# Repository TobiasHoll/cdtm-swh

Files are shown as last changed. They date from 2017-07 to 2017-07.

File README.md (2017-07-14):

# Interactive Beerpong Table (Single Player)

An interactive beerpong game that allows to play beerpong in an arcade game style.

## Description
The interactive beerpong table allows a player to play beerpong (without actual beer) in a normal beerpong set-up. The game is for single players (or players taking turns), because only one side of the beerpong table is built.
A green light within the cups indicates where the player needs to hit. If he succeeds, an alcohol shot is released automatically from the dispenser. Different game logics can be programmed in order to have different levels of difficulties.

## Gameplay

3 cups are lit up green and 7 are lit up red. The cups colours change every 4 secods to make it more difficult. If you hit a green cup, a shot is dispensed. If not you can throw again (3 balls normally)

<p align="center"><a href="https://www.youtube.com/watch?v=cWcqSVTLIn0">
  Beerpong-machine
</a></p>

## Components and where to get them
### Beerpong Box
* Hardware
    * [Arduino](https://store.arduino.cc/arduino-leonardo-with-headers)
    * [Additional 5V Power source](https://www.sparkfun.com/products/12977)
    * [Breadboard](https://www.sparkfun.com/products/12615)
    * [LEDs to light up the cups](http://www.ebay.com/itm/10-1000pcs-WS2812B-5050-RGB-LED-no-PCB-Board-1-LED-Module-Pixel-Light-5V-/221989107317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)
    * [Infra-red sensor for ball detection](https://www.ebay.com/p/10pcs-IR-Infrared-Obstacle-Avoidance-Sensor-Module-for-Arduino-Smart-Car-Robot/1149951524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)
    * [A lot of wires](https://www.conrad.de/de/raspberry-pi-verbindungskabel-rb-cb1-25-1192229.html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)
* Material
    * Wooden panels (2x 45cm*40cm, 1x 40cm*40c)
    * Additional Power Source for the Stepper (depends on the stepper, we used an old ac-adapter)
    
* Material
    * Wooden panels (2x 45cm\*40cm, 1x 40cm\*40cm, 1x 39cm\*40cm)
    * Wooden blocks (4x 5cm\*5cm\*15cm)
    * Lego Technics (check out the video)

## Assembly of the Beerpong-box

Check out the [Youtube video](https://www.youtube.com/watch?v=cWcqSVTLIn0) to see how it's built. This should provide you with enough details, so you can reproduce it.

### Cups (repeat this 10 times) 
* Wire up 3 LEDS per cup
* Remove the bottom of the cup and make 3 holes for the LEDs into it (We used a hot needle)
* Attach the LEDs with hot glue
* Remove the head and the bottom from one bottle
* Make a hole into the side of the bottle (for the sensor)
* Attach the bottle to the bottom of the cup with hot glue
* Attach the IR-Sensor to hole in the bottle (again with hot glue)
In the end it should look like this:

### Box

Our box is 45cm\*40cm\*40cm big, which means you need at least 4 pieces of wood. 

* Build a wooden box with only 4 sides (top and three walls), so you can access the cups easier
* Make holes for the cups into the top of the box. We used a holesaw for that.
* For the door simply attach a wooden panel (slightly smaller than the sides of the box) with a hinge to the box

### Wiring it up
* Put all the cups into the holes in the box
* Connect all the LED-wires, so they are in a row (ends can hang loose)
* Connect the beginning of the LED-wire-row to the Arduino
* Connect all the Power and Ground wires from the IR-Sensors with each other so they're also all in a row
* Attach the Power and Ground beginnings of the Sensor Wiring to your additional power source (we used an USB-cable for that)
* Connect the IR-Data Pin with the Arduino (we used the breadboard for this)
* Connect the ground of the additional power source with the ground of the arduino
* Attach the arduino to the wooden box (together with the breadboard)

Important! Secure the connections of all the wires and attach them to the box if possible.

## Assembly of the Dispenser

### Dispenser
1. Bottle container
* Build  wooden tower which has inner dimensions of the bottles you want to dispense
* A the bottom of the towerm cut out some wood (height of one bottle) on two sides
* Attach the tower to a wooden plate

### Bottle-pushing Mechanism
This one is a bit tricky and really depends on the stepper motor you are using, the height of your bottle and the thinkness of the wood you're using. So here are important aspects to make it work as smooth as possible:
* The bottle-pusher should have the height of one bottle
* The rack needs to be long enough, so the pusher can move forward until the end of the tower and back to the beginning
* The rack should run as smooth as possible, which really depends on the height of the pusher
* The connection of the stepper and the Lego parts is done with a standard [Lego piece (hole in the middle)](http://img.brickowl.com/files/image_cache/larger/lego-yellow-technic-brick-1-x-2-with-hole-3700-30-64503-93.jpg) and some pressure and hot glue 

### Wiring it up

We used an EasyDriver v4.4 to control the stepper motor. To provide enough power to the motor, we wired up a separate power source to the EasyDriver's PWR IN ports. Then, connect the motor to the board and the three STEP pins to the Arduino - make sure that you have enough cable to connect the EasyDriver (which will be part of your dispenser) to the Arduino (which is mounted in the wooden box alongside the cups).

Here, you can see an overview of the wiring. Make sure that the pins for the IR sensors align with the order in which the cups' LEDs are connected - otherwise, adapt the `IRPINS` array in `swh.ino` so that `IRPINS[0]` refers to the pin used for the first cup and so on:

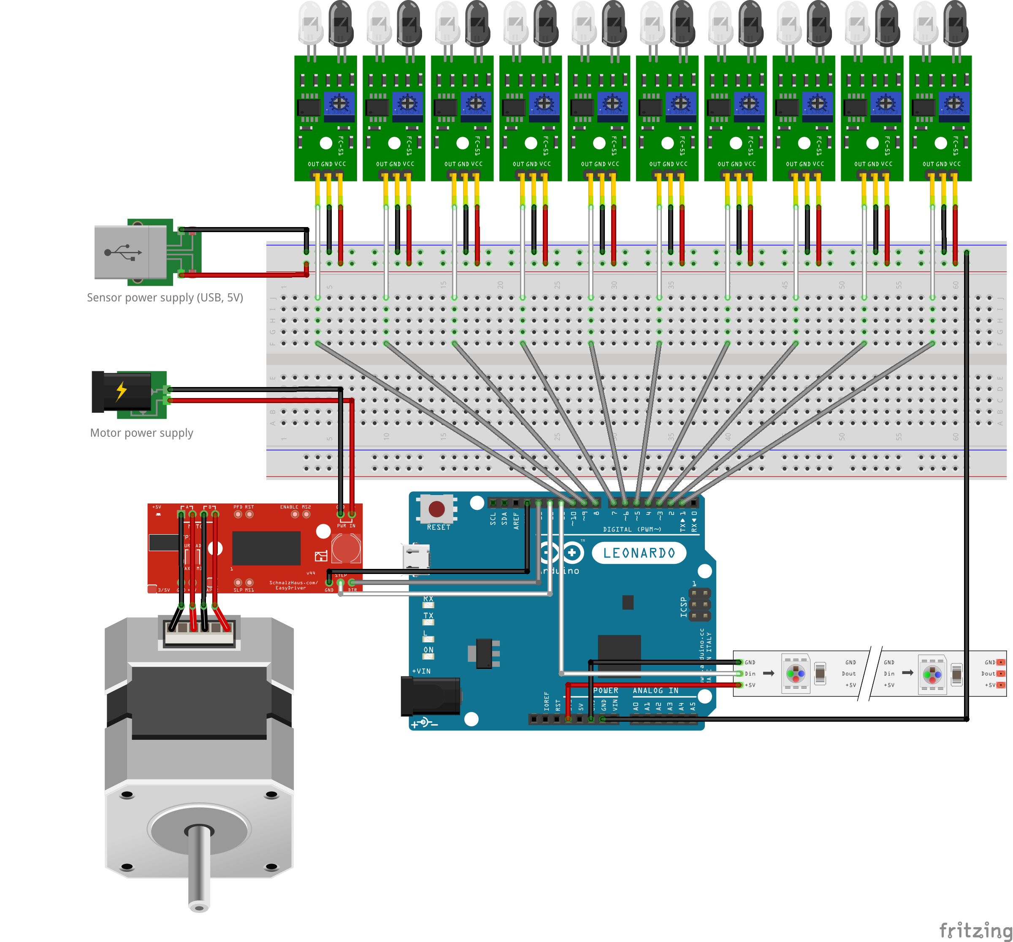
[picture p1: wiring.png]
Wiring diagram


## Software
You just need the [Arduino IDE](https://www.arduino.cc/en/main/software) and the [Adafruit Neopixel Library](https://github.com/adafruit/Adafruit_NeoPixel). After that, just load the `swh.ino` sketch and you're good to go.

## Authors

Tobi, Lisa, Maxim, and Flo; see also the [list of contributors](https://github.com/cdtm-swh/cdtm-swh/graphs/contributors) who participated in this project.

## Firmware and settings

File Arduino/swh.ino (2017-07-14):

#include <Adafruit_NeoPixel.h>
#ifdef __AVR__
  #include <avr/power.h>
#endif

// Game settings
constexpr int TICK_MSEC    =     1;
constexpr int CYCLE_TICKS  =  4000;
constexpr int FLASH_COUNT  =     3;
constexpr int FLASH_TICKS  =   500;
constexpr int TARGET_CUPS  =     3;

// Cup count
constexpr int CUPS = 10;

// Pins
constexpr int IRPINS[CUPS] = {2, 1, 4, 3, 6, 7, 5, 8, 9, 10}; // IR sensor data pins
constexpr int LEDPIN       = 11;                              // LED strip data pin
constexpr int MOTORPIN     = 12;                              // Motor pin
constexpr int DIRECTIONPIN = 13;                              // Motor direction pin
constexpr int SEEDPIN      = A0;                              // Unoccupied analog pin used for random seed

// Motor settings
constexpr int MOTOR_STEPS        = 1800;
constexpr int MOTOR_DELAY_US     = 300;
constexpr int DIRECTION_OUTWARDS = HIGH;
constexpr int DIRECTION_INWARDS  = LOW;

// NeoPixel strip and utilities
constexpr int LEDS_PER_CUP = 3;
Adafruit_NeoPixel strip = Adafruit_NeoPixel(CUPS * LEDS_PER_CUP, LEDPIN, NEO_GRB + NEO_KHZ800);

void setCupColor(int cup, int r, int g, int b)
{
  for (int i = cup * LEDS_PER_CUP; i < (cup + 1) * LEDS_PER_CUP; ++i)
    strip.setPixelColor(i, strip.Color(r, g, b));
}
void setAllColors(int r, int g, int b)
{
  for (int i = 0; i < CUPS * LEDS_PER_CUP; ++i)
    strip.setPixelColor(i, strip.Color(r, g, b));
}
void updateStrip()
{
  strip.setBrightness(255);
  strip.show();
}
void disableStrip()
{
  strip.setBrightness(0);
  strip.show();
}
void toggleStrip()
{
  strip.setBrightness(255 - strip.getBrightness());
  strip.show();
}

void flashBlock(int r, int g, int b)
{
  // Preserve original colors
  uint32_t originalColors[CUPS * LEDS_PER_CUP];
  for (int i = 0; i < CUPS * LEDS_PER_CUP; ++i)
    originalColors[i] = strip.getPixelColor(i);

  // Update all colors and flash
  for (int i = 0; i < FLASH_COUNT; ++i)
  {
    setAllColors(r, g, b);
    updateStrip();
    delay(TICK_MSEC * FLASH_TICKS);
    setAllColors(0, 0, 0);
    updateStrip();
    delay(TICK_MSEC * FLASH_TICKS);
  }

  // Restore colors
  for (int i = 0; i < CUPS * LEDS_PER_CUP; ++i)
    strip.setPixelColor(i, originalColors[i]);
  updateStrip();
}

void moveDispenser(int dir)
{
  for (int i = 0; i < MOTOR_STEPS; ++i)
  {
    digitalWrite(DIRECTIONPIN, dir);
    digitalWrite(MOTORPIN, HIGH);
    delayMicroseconds(MOTOR_DELAY_US);
    digitalWrite(MOTORPIN, LOW);
    delayMicroseconds(MOTOR_DELAY_US);
  }
}

void dispense()
{
  moveDispenser(DIRECTION_OUTWARDS);
  moveDispenser(DIRECTION_INWARDS);
}

// Data types
enum class event
{
  NONE,
  FLASH_WRONG,
  FLASH_CORRECT,
};

// Setup
void setup() {
  // Set up serial connection
  Serial.begin(9600);

  // Set up pin mode
  pinMode(LEDPIN, OUTPUT);
  pinMode(MOTORPIN, OUTPUT);
  pinMode(DIRECTIONPIN, OUTPUT);
  for (int index = 0; index < CUPS; ++index)
    pinMode(IRPINS[index], INPUT);

  // Set up LED strip
  strip.begin();
  disableStrip();

  // Seed RNG
  randomSeed(analogRead(SEEDPIN));
}

// Main loop
void loop()
{
  static int tickInCycle = 0;
  static int currentTargets[TARGET_CUPS] = {0, 0, 0};

  if (tickInCycle == 0)
  {
    // New cycle, select next target
    if (TARGET_CUPS == 1)
    {
      int nextTarget = currentTargets[0];
      while (nextTarget == currentTargets[0]) nextTarget = random(CUPS);
      currentTargets[0] = nextTarget;
    }
    else
    {
      for (int target = 0; target < TARGET_CUPS; ++target)
      {
retry:
        int nextTarget = random(CUPS);
        for (int other = 0; other < target; ++other)
          if (nextTarget == currentTargets[other])
            goto retry;
            
        currentTargets[target] = nextTarget;
      }
    }

    // Update cup colors
    setAllColors(255, 0, 0);
    for (int target = 0; target < TARGET_CUPS; ++target)
      setCupColor(currentTargets[target], 0, 255, 0);
    updateStrip();
  }

  // Check the IR sensors for events
  event evt = event::NONE;
  for (int index = 0; index < CUPS; ++index)
  {
    if (digitalRead(IRPINS[index]))
    {
      for (int target = 0; target < TARGET_CUPS; ++target)
      {
         if (index == currentTargets[target])
         {
           evt = event::FLASH_CORRECT;
           break;
         }
         else evt = event::FLASH_WRONG;
      }
      break;
    }
  }
  
  switch (evt)
  {
    case event::FLASH_CORRECT:
      flashBlock(0, 255, 0);
      setAllColors(0, 255, 0);
      updateStrip();
      dispense();
      tickInCycle = CYCLE_TICKS - 1;
      break;
    case event::FLASH_WRONG:
      flashBlock(255, 0, 0);
      tickInCycle = CYCLE_TICKS - 1;
      break; 
  }
  
  // Tick.
  tickInCycle = (tickInCycle + 1) % CYCLE_TICKS;
  delay(TICK_MSEC);
}

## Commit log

2017-07-11 IR feedback to LEDs
2017-07-14 Updated documentation
    [wiring.fzz]
